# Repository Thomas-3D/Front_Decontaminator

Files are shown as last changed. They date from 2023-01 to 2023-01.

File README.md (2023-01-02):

# Front Decontaminator
# !!! work in progress !!!

This mod adds a nozzle brush and a purge bucket to Voron 2.4 printer's front side. It is a variation of the famous Decontaminator Purge Bucket & Nozzle Scrubber by edwardyeeks, it does the same thing but on the front.

https://github.com/VoronDesign/VoronUsers/tree/master/orphaned_mods/printer_mods/edwardyeeks/Decontaminator_Purge_Bucket_&_Nozzle_Scrubber

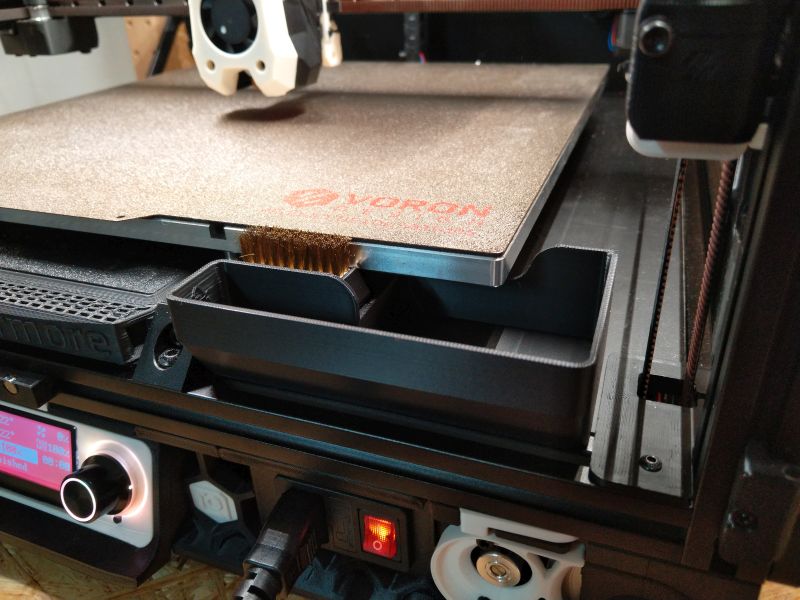
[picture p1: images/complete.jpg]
complete


The parts don't collide with Nevermore Filter mod.

## But why on the front?
cons: 
- You need to remove your Z-endstop and move the bed to the back, so you need the new TAP toolhead
- bucket is only on one side of the brush
- you can see dirt in the bucket

pro:
- You can see dirt in the bucket
- easier to empty the bucket, no matter where the toolhead is parked

## BOM

**Brush Holder**
Size | Qty
--- | ---
M3x4-16 SHCS | 2
M3x10 SHCS | 2
M3 T-Nut | 2
Ø6x3 Magnet | 2
copper brush | 1

The two screws for the bucket need to be magnetic and can be longer. The screwholes are open on the underside.

## Printed parts

These parts are close to the heated bed, I used ABS with standard Voron settings. This is:
- 0.4mm nozzle
- 0.2mm layer height
- 40% infill
- no supports necessary
- 4 perimeters
- 5 top and bottom layers

The parts are designed for the front-right side. For the left side mirror the parts in your slicer.

## LDO-kit specific parts

LDO ships longer bed spacers with their V2.4 kits, the printed parts need to be higher.

## Changes in printer.cfg

for my(!) 350 build:
- [stepper_y]
- ...
- position_min: -7  # this is where the toolhead touches the front door
- position_endstop: 350
- position_max: 350

[include nozzle_scrub.cfg]
- modify nozzle_scrub macro

## Installation

- make changes to printer.cfg
- loosen bed screws
- home and move printhead to Y=0
- align the front edge of the buildplate with your nozzle
- install magnets to brush holder (if they are loose you can glue them in afterwards through holes in the top)
- cut brush to 40mm and press it in brush holder
- mount brush holder with 2x M3x10 and T-nuts to the side of the bed extrusion
- screw 2x SHCS in the bucket, threads are printed in

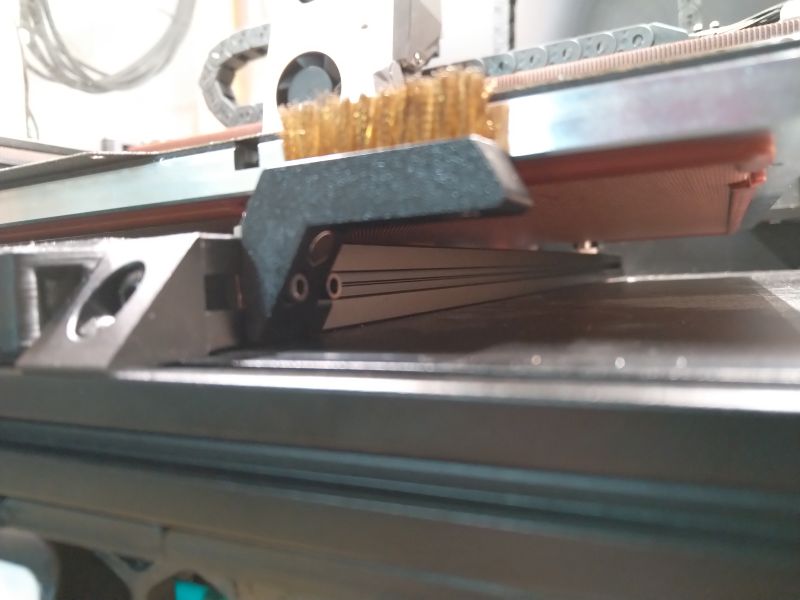
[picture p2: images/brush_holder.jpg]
brush_holder


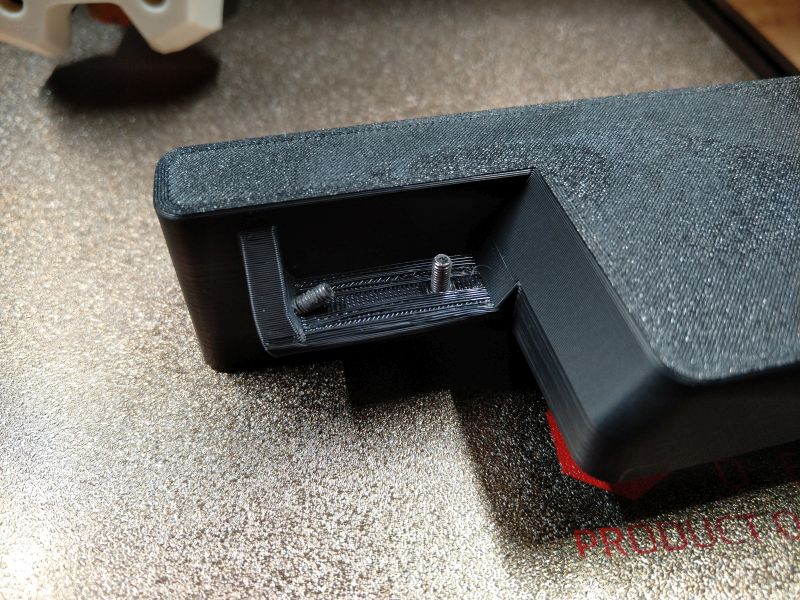
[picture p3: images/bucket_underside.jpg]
bucket_underside


## Testing and feedback

I can only verify the 350mm LDO version works. Please give me feedback if your version works or how it can be improved.

Tag me on Voron Discord: Justheretolookpretty#3570

Have fun!

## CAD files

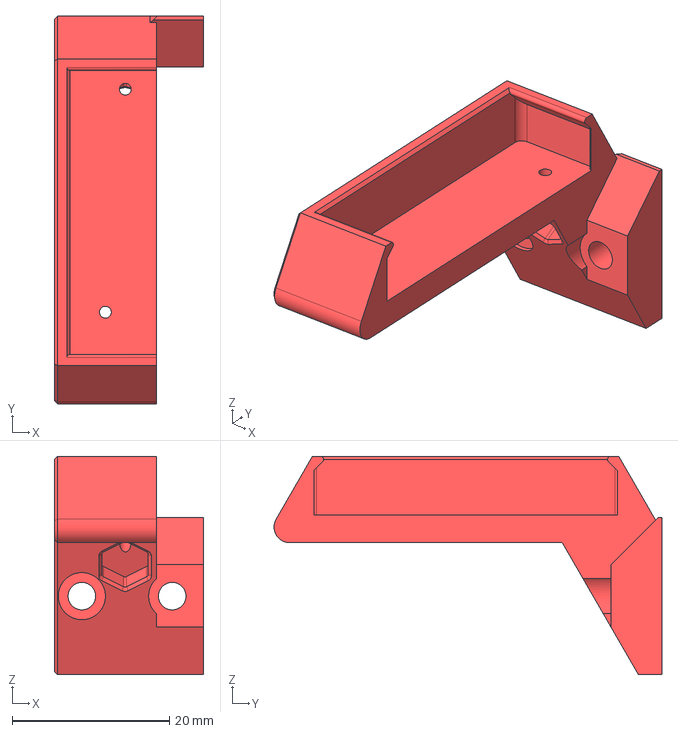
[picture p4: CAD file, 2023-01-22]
CAD/Brush Holder.step
19.0 x 49.4 x 27.8 mm

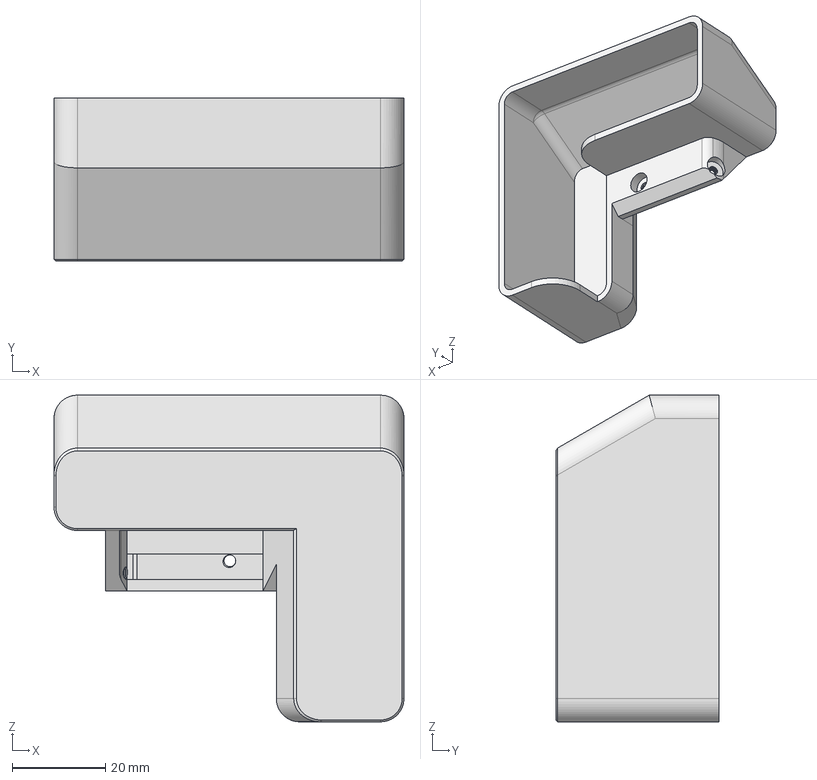
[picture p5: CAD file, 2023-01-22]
CAD/Bucket250.step
75.0 x 35.0 x 70.0 mm

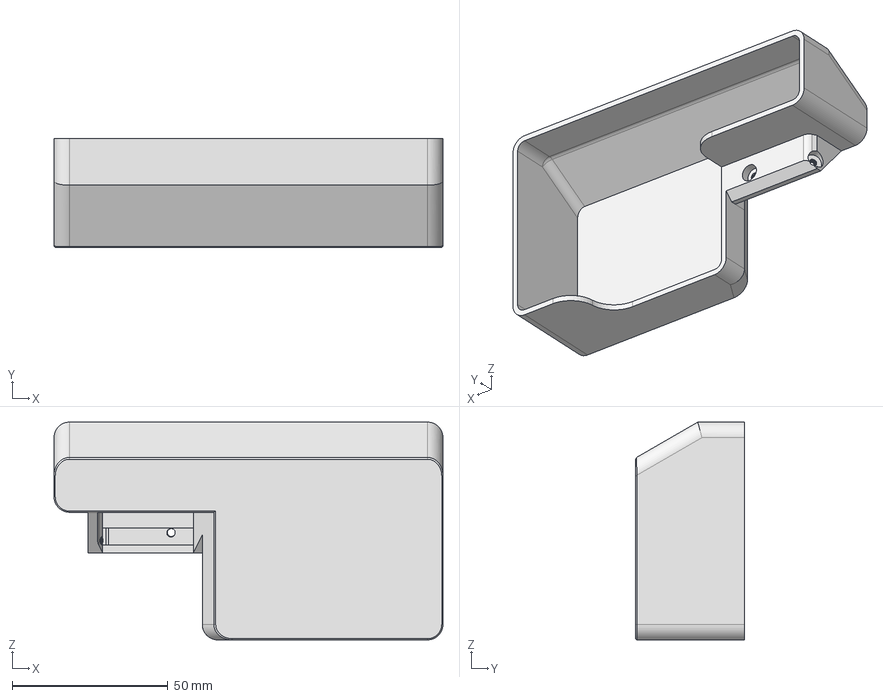
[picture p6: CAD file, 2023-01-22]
CAD/Bucket350.step
125.0 x 35.0 x 70.0 mm

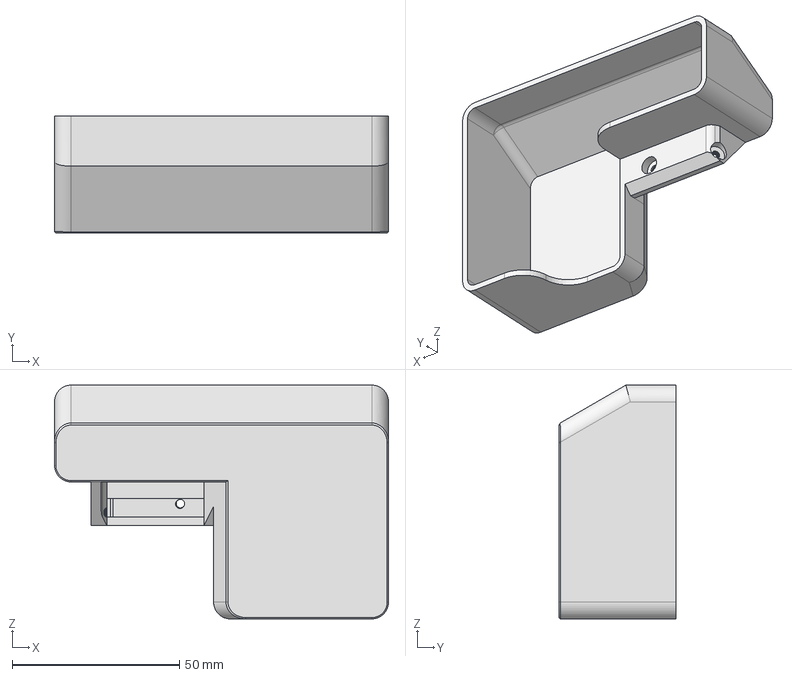
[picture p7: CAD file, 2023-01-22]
CAD/Bucket300.step
100.0 x 35.0 x 70.0 mm

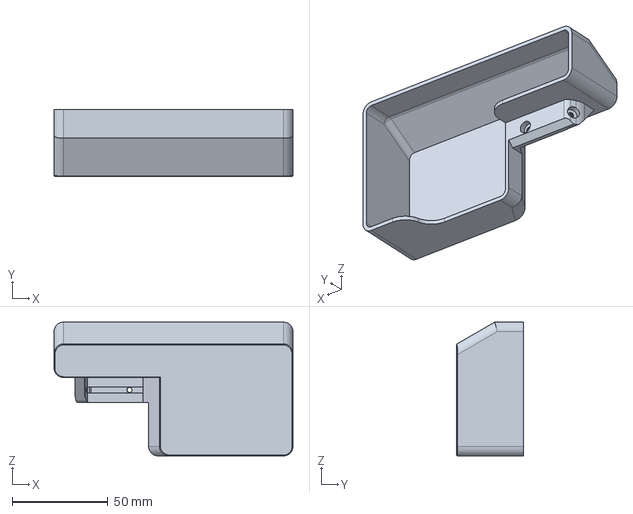
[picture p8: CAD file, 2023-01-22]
CAD/Bucket350_LDO.step
125.0 x 35.0 x 70.0 mm

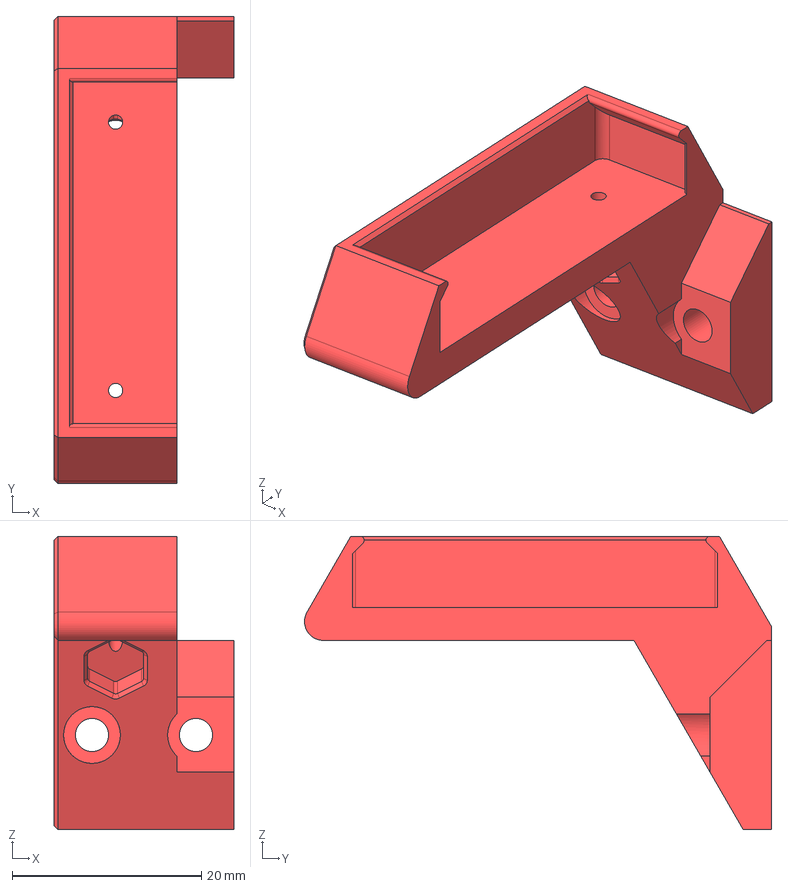
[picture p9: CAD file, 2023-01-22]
CAD/Brush_Holder_LDO.step
19.0 x 49.4 x 31.0 mm

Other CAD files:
CAD/Bucket250_LDO.step
CAD/Bucket300_LDO.step
STL/Brush_Holder.stl
STL/Brush_Holder_LDO.stl
STL/Bucket250.stl
STL/Bucket250_LDO.stl
STL/Bucket300.stl
STL/Bucket300_LDO.stl
STL/Bucket350.stl
STL/Bucket350_LDO.stl

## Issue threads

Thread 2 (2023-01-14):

Too short for kinetic bed mounts

crashmaxx, 2023-01-14:
I need to make the brush holder about 10mm higher than the standard part for my bed with kinetic mounts. I can make the changes if you share a STEP file.

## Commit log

2023-01-02 upload STLs
    [Brush Holder.stl, Brush_Holder_LDO.stl, Bucket250.stl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]
2023-01-02 file name
    [Brush_Holder.stl]
2023-01-22 add CAD
    [Brush Holder.step, Brush_Holder_LDO.step, Bucket250.step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]
